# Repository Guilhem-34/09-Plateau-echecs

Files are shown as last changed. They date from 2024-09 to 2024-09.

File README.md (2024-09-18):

# High-Tech-Chess Project (In Progress)
###### {Polytech Montpellier Third year Project}

Second project of the year, currently in progress and the biggest project I've worked for !

## Introduction

Chess is a game that transcends time. That's why we wanted to innovate by using modern technologies to make the game experience more futuristic. 

What if I tell you that it's possible to play chess from a distance while physically moving pawns. This is currently our goal by making an automatic mechanism which takes in input the XY coordinates and then move the pawn.

here's how the game would be played :

   - The 1st player move his pawn and the system copy the movement in the 2nd player's chessboard.
     
   - After the movement being done, it's the 2nd player's turn, doing the same thing as the 1st player.

## Visuel
<div align="center">
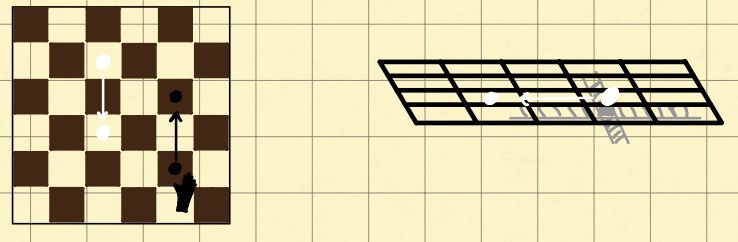
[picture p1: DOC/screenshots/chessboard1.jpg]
  
</div>

## More technically

### Board mechanism

For chess pieces, we have pieces with a magnetic disk at the base, easily found in supermarkets or on the Internet. We decided to use this feature and move them with an electromagnet by using electromagnetic force.

So we're going to use a mechanical system that moves along the carthesian plane. We're thinking in terms of a system using stepper motors, pulleys and timing belts, in the same way as CNC systems.

<div align="center">
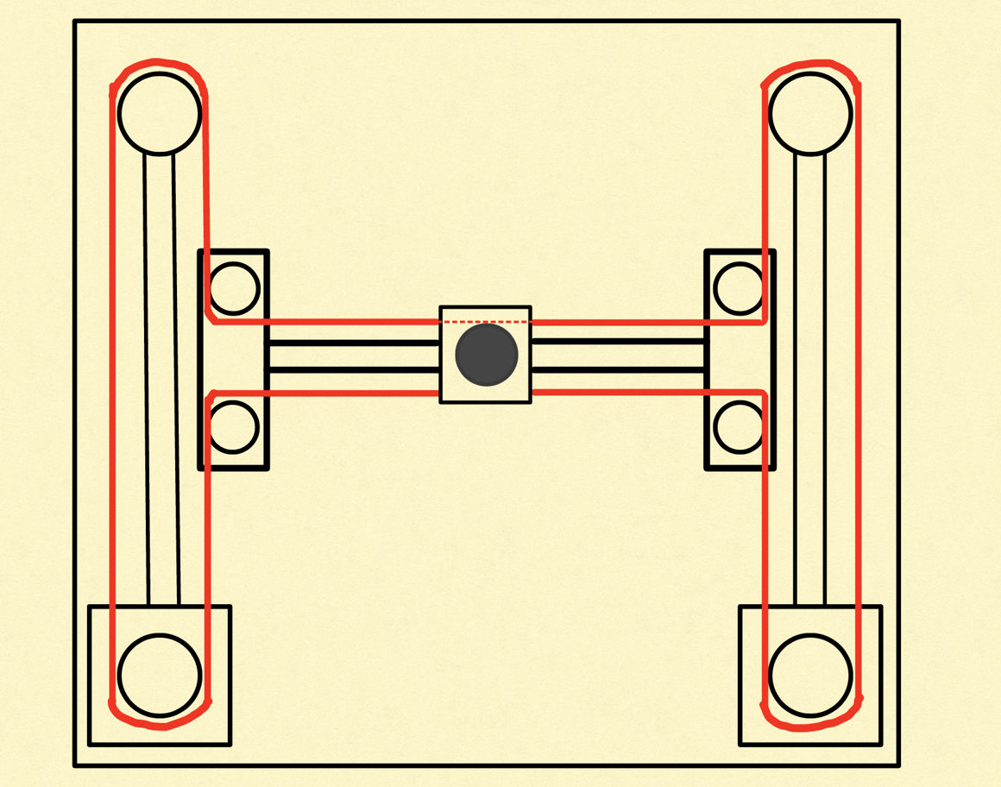
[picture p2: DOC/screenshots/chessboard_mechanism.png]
  
</div>

As someone who really likes projects needing at the same time elctronics, IT and mechanics (i.e. Mecatronic), I'm very excited to see the final result !

### Pawns detections

We have several tools and ways to detect the presence of the pawn but our first idea is to use Hall effect sensors which detects the presence of the pawn thanks to theirs base's magnet disk.

### The Microcontroller

To control all of this stuff, it'll be necessary to use a Microcontroller. We first thought of using an Arduino but we would like to change of µC because most of our last projects were including an Arduino, we want to discover something else. 

As we're learning a lot about the nucleo board from STM in our µC class, we would like to use it at the end of our project. But we need to be effective because we have a time constraint, so we decided to temporarily use the Arduino board for the tests.

## Features

At the end of our project, the High Tech Chess board will be able of :

- Determine the position of the pieces to be moved.
- From the start and finish coordinates, find the shortest path, avoiding the other pieces.
- Move eliminated pieces to one side of the board.
- Send and receive data over a network for remote play.
- Report all movements using a graphical interface.

**Stay tuned for further project updates !**

<br />
<br />

## 

<br />
<br />

Review of the 1<sup>st</sup> prototype
===========================================================

For 3 months, we worked on various aspects of our project and were able to make a few observations.

<div align="center">
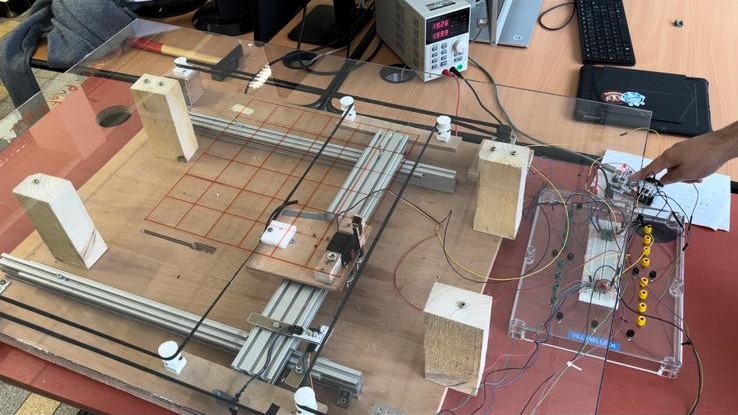
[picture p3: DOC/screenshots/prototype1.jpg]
  
</div>

### Board mechanism

As this is not our core business, we found it very difficult to create a fluid, solid and reliable mechanical system. Indeed, our system had certain imperfections, such as :

- Movement with deviations.
- A belt that wasn't tight enough (the belt therefore wasn't taking all the motor's steps).
- Very fragile pulleys, which were 3D printed.

<div align="center">
  
</div>

### Pawns detections and movement

We thought using an electromagnet to move the pawns but it turned out to be a bad idea because the pawn base's diameter is too short to close the electromagnet's field. Instead, we'll be using a simple magnet which gives more power to attract the pawns. 

### The Microcontroller

As planned from the very beginning, we performed the first tests (stepper motors and servomotor) on the Arduino development board, then wrote the function libraries directly on the STM32 board. 

In the end, the migration to STM32 proved to be an interesting choice, not only because we were able to put our knowledge into practice, but also because we were faster and more reactive. Indeed, the STM's processor frequency is much higher than the Arduino's (48 MHz for the STM32 board vs. 64kHz for the Arduino board).

In terms of code, our program can :

- Move a given number of squares in one direction.
- Go from point A to point B (only if the destination square is empty).
- Display and update the chessboard.
- Detect the interruption of the push buttons when reseting the system position's.

### To sum up

This prototype has a lot of mechanical issues, so we decided to put more efforts into the developpment of a 2<sup>nd</sup> prototype. This one will fix those issues and make it more reliable, lighter and more compact.

At this stage of the project, we're starting to have a lot of wires, so we're planning to do a PCB to make it cleaner. 

We made a lot of mistakes during the developpment of the first prototype but that's part of the process ! 

<br />
<br />

## 

<br />
<br />

Review of the 2<sup>nd</sup> prototype
===========================================================

For the last month, we designed a second prototype which (in theory) will fix the issues encountered on the first prototype.

<div align="center">
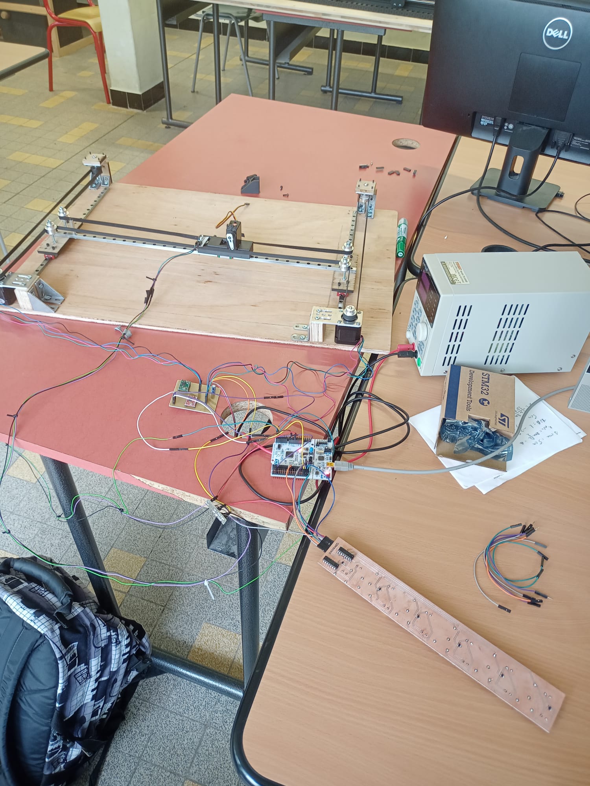
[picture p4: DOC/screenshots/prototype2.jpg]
  
</div>

### Board mechanism

This time, we made the mechanism more quickly and fix some issues but unfortunately, we've run into others issues such as :

- A bad quality of the ball bearing carriages.
- A belt that still wasn't tight enough (the belt therefore wasn't taking all the motor's steps).

However, since the beginning, we've been using a breadboard to link our peripherals to our microcontroller, which is no longer comfortable when we have a lot of cables. So we designed a PCB that makes our workspace cleaner.

<div align="center">
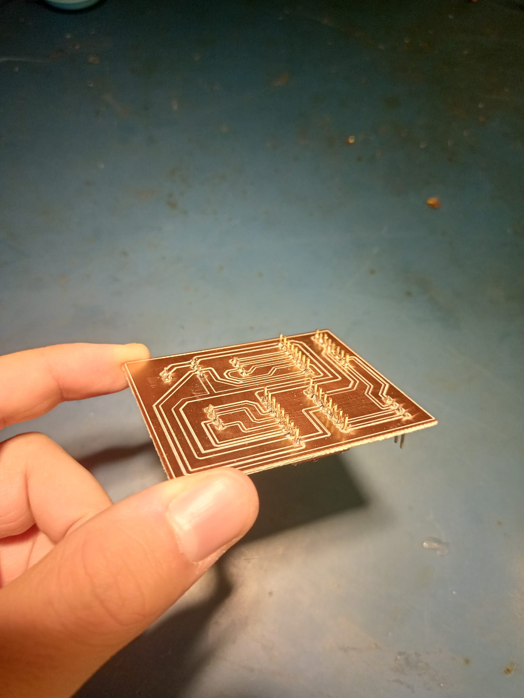
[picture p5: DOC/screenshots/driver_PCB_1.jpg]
  
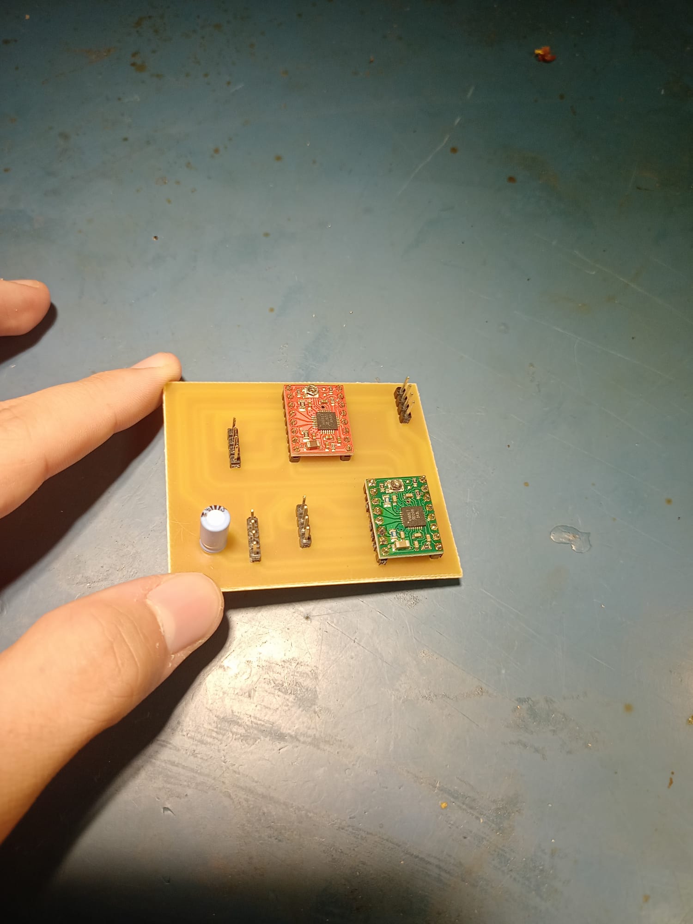
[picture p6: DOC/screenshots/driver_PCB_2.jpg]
  
</div>

### Pawns detections

As soon as we received our hall-effect sensors, we were able to test them and design a PCB. Due to a lack of time, we designed a PCB that recovers the state of each sensor on a single line of our chessboard.

Actually, we used demultiplexors to recover the state of a sensor : one which choose the sensor per line and one who select the line.

<div align="center">
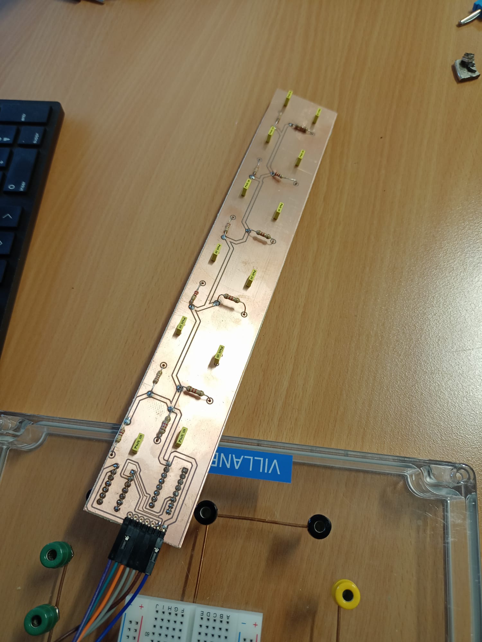
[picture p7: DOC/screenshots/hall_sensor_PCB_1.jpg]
  
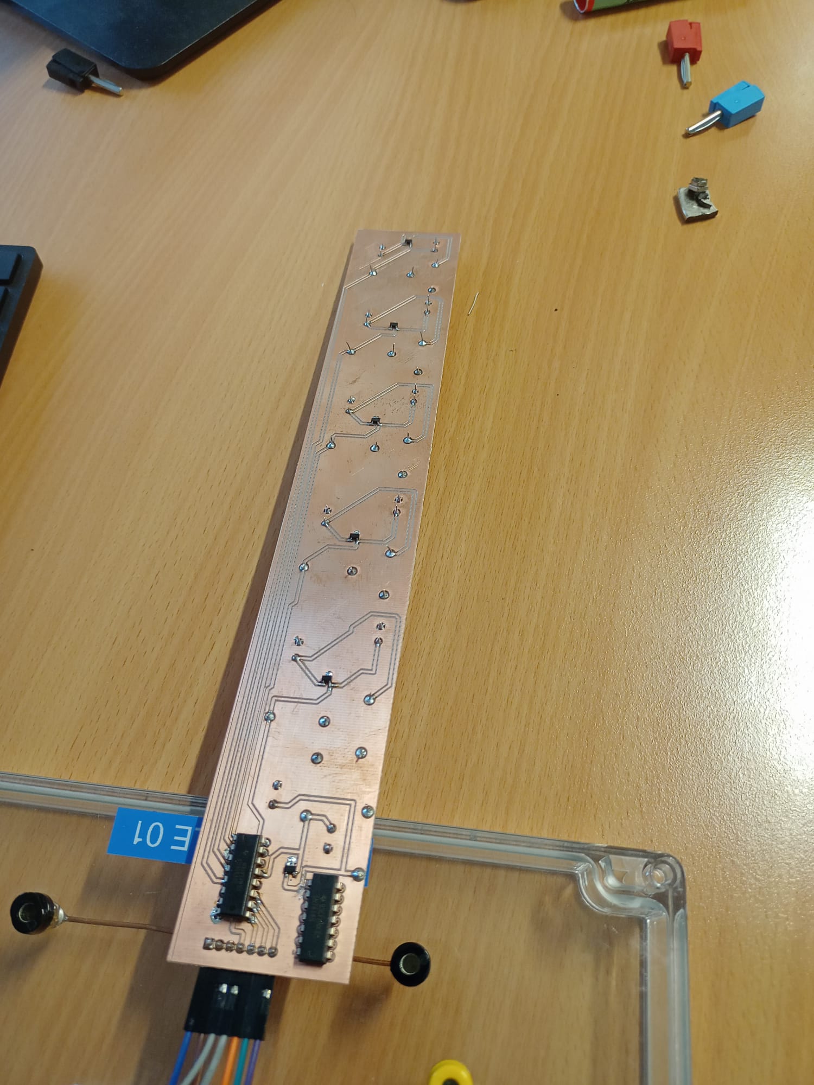
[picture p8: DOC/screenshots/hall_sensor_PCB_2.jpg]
  
</div>

### The Microcontroller

We added some functions to perform the detection through the hall effect sensors. The state of all of the sensors is displayed on a table. It would be interesting to use DMA for making the printing into console more fast and to allow the processor to do something else.

## To sum up

This prototype fixed the previous issues but still have some. Unfortunately, in the rush, we forgot to record a video of the demo.

Finally, if we were to continue this project, our objective would be to:

- Add the Enable pin to the motor drivers to enable them only when we have to move and thus avoid overheating of the motors.
- Design a shield-shaped PCB on our board to make modifications more flexible.
- Avoid lateral play of the main rail by using a T-shaped lateral structure connected to the main rail.
- Replace the demultiplexors with an I2C bus port expansion card.

At the end of this project, we've had a lot of mechanical constraints, but we've also become aware of how difficult it is to manage time. However, this project was full of interesting subjects and we learned so much things !

We'll get back stronger :)

<br/>

_ZAKANI-FADILI Bilel - ASSET Guilhem - AUBERTIN Michael_

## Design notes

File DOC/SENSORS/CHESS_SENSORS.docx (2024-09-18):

ZAKANI-FADILI Bilel

AUBERTIN Michael

ASSET Guilhem

# Choix du type de capteurs

# I. Capteur à effet Hall

## A. Présentation

### Principe : lorsqu'un courant électrique passe à travers un conducteur et qu'un champ magnétique est appliqué perpendiculairement à ce conducteur, une différence de tension se produit sur les côtés du conducteur. C’est l’effet Hall.

### Lorsqu'un champ magnétique externe est présent et qu'il coupe le conducteur, cela crée une différence de tension sur les côtés du conducteur, selon l'effet Hall. C’est cette tension qui est détectée par le capteur.

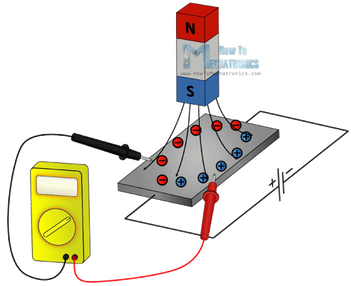
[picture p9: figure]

Après plusieurs recherches de différents capteurs, nous décidons de choisir le capteur TLE 4935 (https://www.conrad.fr/fr/p/infineon-technologies-capteur-a-effet-hall-tle-4935-l-3-5-24-v-dc-plage-de-mesure-10-20-mt-psso-3-2-a-so-153775.html) qui possède une plage de tension de 3,5 à 24 V et une plage de mesure de +10 à +20 mT, ces caractéristiques s’accordent bien avec nos besoins. Ce capteur se révèle également intéressant par son prix (0,76€ l’unité) en fonction du nombre de capteurs nécessaire.

## B. Méthode d’utilisation

Comme notre capteur doit pouvoir récupérer la position de chaque pièce sur l’échiquier, notre première idée et la plus simple est de placer un capteur à effet hall sous chaque case. On vient placer une surface plane avec nos capteurs en dessous de notre échiquier. Cette méthode permettrait d’avoir l’état de chaque case en temps réel (libre ou occupé). En revanche, comme il y a 96 cases qui peuvent accueillir les pions (64 cases jouables + 32 cases pour les pièces mangées), il faudrait donc utiliser 96 capteurs à effet hall. Comme évoqué précédemment, le capteur est avantageux à partir du moment où il est utilisé en petite quantité, contrairement à notre cas. Il faudrait débourser 72€ de capteurs ce qui est inenvisageable et rendrait le prix final du produit beaucoup trop cher.

### Nous cherchons donc une méthode pour diminuer le nombre de capteurs tout en apportant les mêmes fonctionnalités. Pour cela, nous avons pensé à deux méthodes :

### Electroaimant entouré de capteurs :

Cette méthode consiste à placer les capteurs autour de l’électroaimant. De cette manière, 8 capteurs suivent le déplacement du système mécanique et c’est celui-ci qui va se déplacer comme un serpent sur tout l’échiquier entre chaque action pour identifier l’état des cases. En revanche, cette méthode peut se révéler relativement lente et surtout très complexe à coder. En effet, si le système parcourt l’échiquier, plusieurs capteurs peuvent être amenés à identifier la même case à intervalles de temps différents. Il faut donc pouvoir accepter la mesure de certains capteurs et en rejeter d’autres.

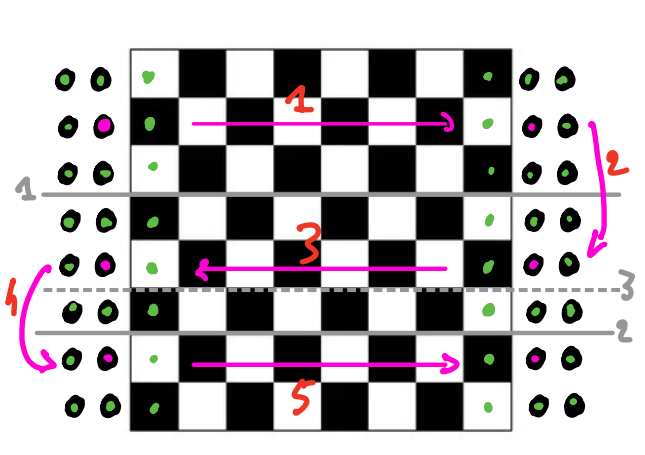
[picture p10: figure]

##### 1. Translation de 9 cases vers la droite

##### 2. Translation de 3 cases vers le bas

##### 3. Translation de 9 cases vers la gauche

##### 4. Translation de 2 cases vers le bas

##### 5. Translation de 9 cases vers la droite

### Fig 1. Déplacement du système principal entouré des capteurs

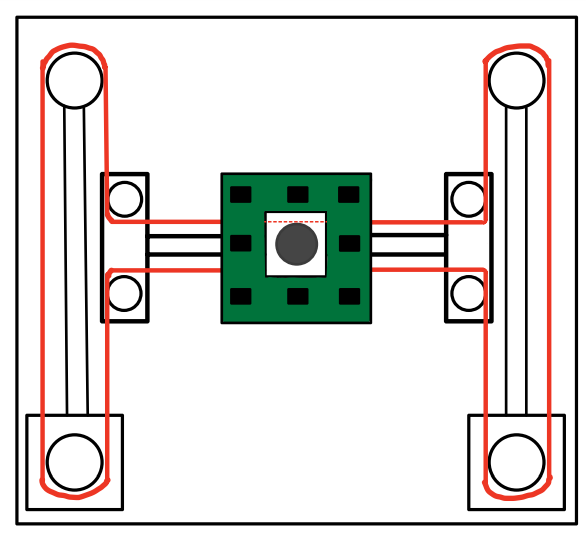
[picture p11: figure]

### Fig 2. Vue d’ensemble du système principal entouré des capteurs

### Barrette de capteurs accroché à la structure principal :

Cette méthode s’inspire de la précédente où cette fois l’objectif est de scanner chaque case une seule fois. Elle doit également garder un faible nombre de capteurs. Nous nous sommes donc inspirés du mécanisme de photocopie d’une imprimante. En effet, une barrette lumineuse effectue un seul déplacement dans un sens pour venir photocopier la feuille de papier. Le principe est le même, une barrette de 10 capteurs accrochée à la structure principale (qui se déplace uniquement linéairement) va venir scanner toutes les cases en un seul mouvement. Cette façon de faire simplifie le traitement des données tout en simplifiant le mouvement.

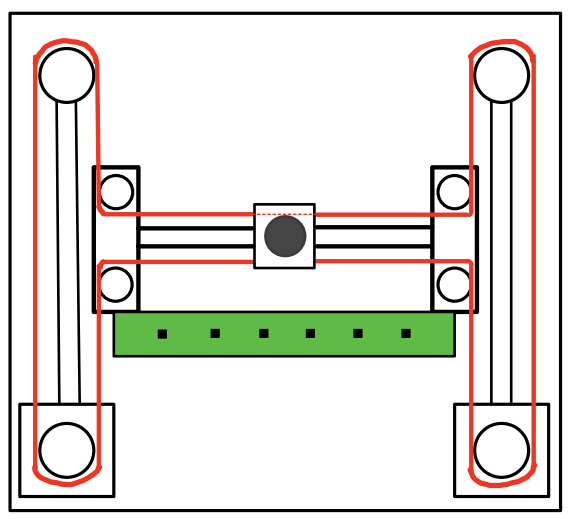
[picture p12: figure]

### Fig 3. Vue d’ensemble avec la barrette de capteurs

# II. Capteur de force FSR

## A. Présentation

### Principe : Un capteur de force FSR est un capteur plat, flexible, qui permet de mesurer la force en fonction de la pression qui y est appliquée : F=P*S

Il faut savoir que les capteurs de force ne permettent pas une lecture immédiate. En effet, il faut les étalonner à l’aide de charges de références. Les résistances de mesure de force reposent sur une technologie de piézorésistive. Autrement dit, ce sont des éléments passifs qui se comportent en résistance variable dans un circuit électrique. Comme le montre la figure 4, lorsqu'il n'est pas sollicité, le capteur présente une résistance élevée, de l'ordre de quelques mégaohms (MΩ), qui diminue lorsqu'une force est appliquée, généralement de l'ordre de quelques kiloOhms (KΩ). Si l'on considère l'inverse de la résistance (conductance), la réponse du capteur en fonction de la force appliquée est proportionnelle dans la plage de force prévue pour le modèle.

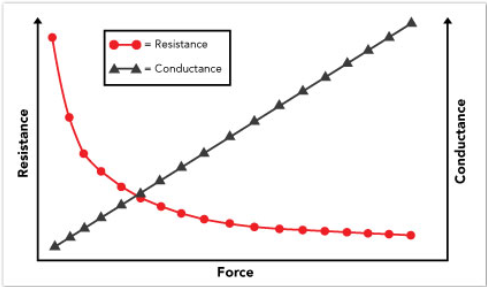
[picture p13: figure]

### Fig 4. Reponse du capteur FSR en fonction de la force

## C. Méthode d’utilisation

### Pour rappel, les capteurs doivent permettre de récupérer la position de chaque pièce sur l’échiquier. Il y a besoin d’un contact entre les pièces d’échecs et les capteurs, il faudrait placer un capteur sous chaque case, de la manière que la première méthode avec les capteurs à effet Hall.

# III. Antenne NFC

## A. Présentation

### Principe : un tag NFC fonctionne avec une technologie proche de l’induction. Le tag NFC est composé d’une antenne et d’une mémoire. L’antenne relais va émettre un champ magnétique qui va alimenter le tag et donc émettre son contenu en mémoire.

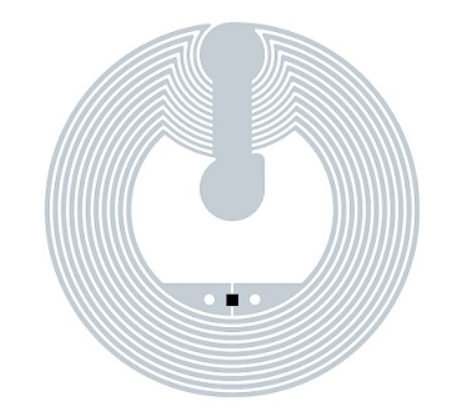
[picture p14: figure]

### Fig 5. Tag NFC

## D. Méthode d’utilisation

Cette méthode est plus particulière car elle consiste à placer un tag NFC sous chaque pièce. Le plateau d’échecs va ensuite être analysé à l’aide d’une antenne NFC accroché au système principal. De cette manière, on pourrait récupérer la position de chaque pièce en « scannant » toute les cases. Chaque pièce serait donc associée au contenu mémoire de son tag NFC.

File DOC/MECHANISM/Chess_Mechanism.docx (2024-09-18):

Asset Guilhem

Aubertin Michaël

Zakani Bilel

Mécanisme de la table

Le point de départ de notre projet reposait sur la partie mécanique, nous devions étudier les différents mécanismes qui nous permettraient de déplacer les pièces une fois la commande ordonnée par notre code. Le principe étant de pouvoir atteindre un point avec des coordonnées x et y, nous avons eu l’idée d’utiliser une machine à commande numérique (CNC).

Choix du type de CNC :

1. Core XY

La structure CNC la plus connue est le Core XY, elle est grandement utilisée dans les systèmes d’impression 3D et dans les tables d’usinage. Elle permet d’atteindre des coordonnées x et y mais ne permet pas de se déplacer selon l’axe en z.

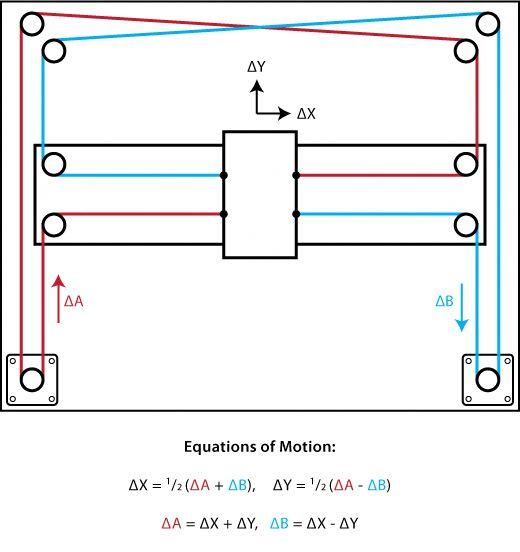
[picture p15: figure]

Schéma 1 : Core XY

A : Principe de fonctionnement

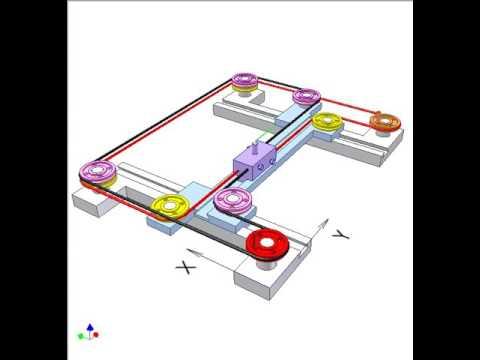
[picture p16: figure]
Controlling two linear motions of an object 3

Vidéo n°1 : Fonctionnement Core XY

Les mouvements dans le plan de la structure violette le long des axes X et Y sont contrôlés par les moteurs symbolisés dans cette vidéo par les roues rouges et oranges.

La courroie dentée noire est fixée à la plateforme violette. Elle permet de relier la roue rouge aux poulies roses.

La courroie crantée rouge est-elle aussi fixée à la plateforme. Elle relie la roue orange aux poulies jaunes.

Lorsque les moteurs rouge et orange tournent en sens inverse à la même vitesse, l'objet se déplace le long de l'axe X.

Lorsque les moteurs tournent dans le même sens à la même vitesse, l'objet se déplace le long de l'axe Y.

Lorsqu'un seul des deux moteurs tourne, l'objet violet se déplace en diagonale.

B. Avantages et inconvénients :

Points positifs :

- Précision : Le système Core XY offre une haute précision de mouvement grâce à la séparation des moteurs pour chaque axe.
- Vitesse : Ils peuvent atteindre des vitesses élevées en raison de la conception du mouvement parallèle.
- Stabilité : La structure est plus stable, ce qui peut minimiser les vibrations.

Points contraignants :

- Complexité : La mise en place et la maintenance d'un système Core XY peuvent être plus complexes en raison du nombre de composants. Une des difficultés principales sera d’aligner parfaitement la hauteur des roulements avec les différents moteurs.
- Coût : Ce système peut être plus coûteux à construire en raison du matériel supplémentaire nécessaire.

2. H-Bot

Le système H-Bot est une variante du système Core XY, cependant il possède des spécificités qui pourraient être particulièrement intéressantes pour notre projet.

A : Principe de fonctionnement :

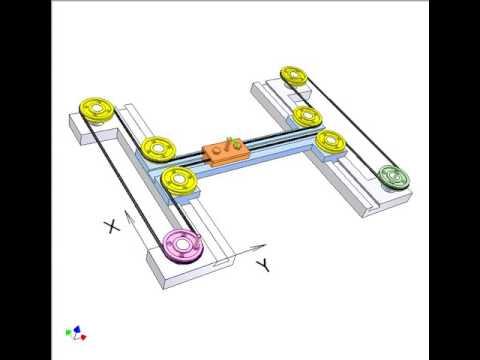
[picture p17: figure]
Controlling two linear motions of an object 1a

Vidéo n°2 : Fonctionnement H-Bot

Les mouvements de la structure orange le long des axes X et Y sont contrôlés par les moteurs représentés ici par les poulies rose et verte.

Une branche de la courroie noire est fixée au bloc orange, l'autre le traverse.

Lorsque les poulies rose et verte tournent dans des directions opposées à la même vitesse, l'objet se déplace le long de l'axe X.

Lorsque les poulies rose et verte tournent dans le même sens à la même vitesse, l'objet se déplace le long de l'axe Y.

B. Avantages et inconvénients :

Points positifs :

- Simplicité : Le système H-Bot est souvent plus simple en termes de conception et de mouvement, ce qui peut faciliter la construction et la maintenance.
- Coût : En général, il peut être moins cher à construire en raison de la conception plus simple.
- Gain de place : Ce système pourrait être particulièrement minimaliste en termes de hauteur notamment.

Points contraignants :

- Précision : Peut avoir une précision légèrement inférieure par rapport aux systèmes Core XY.
- Vitesse : Peut ne pas atteindre les mêmes vitesses que les systèmes Core XY en raison de la conception

3. Système cartésien

Le système CNC cartésien est un système amélioré du Core XY au niveau des déplacements. En effet, il permet un déplacement le long de l’axe X, Y et Z.

A : Principe de fonctionnement :

Le principe de fonctionnement est exactement le même que celui en Core XY, cependant, il permet de se mouvoir également selon l’axe Z à l’aide d’un moteur fixé sur la plateforme.

B. Avantages et inconvénients :

Points positifs :

- Les CNC cartésiennes ont principalement les mêmes points positifs que le CORE XY
- Le point fort principal de ce système est l’accessibilité au déplacement le long de l’axe Z

Points contraignants :

- La vitesse d’exécution de ce système est un peu plus lente que le Core XY
- Le principale point négatif de la machine cartésienne est que la structure principale qui se déplace le long de l’axe X est encombrée d’un moteur dont les branchements doivent être portatifs .

Tableaux de choix :

Insérer tableau

Conclusion :

Pour conclure, grâce à nos différentes recherches, nous avons récolté de nombreuses informations sur les différentes CNC qui nous ont permis de repérer les qualités et défauts de chacune. En prenant compte de nos besoins, nous pensons que la machine idéale serait la H-Bot. Elle nous permettrait d’avoir une solution peu coûteuse , plus facile à construire et surtout elle occuperait moins de place (en hauteur) ce qui permettrait d’être plus discret tout en étant efficace. Nous avons confirmé nos intentions de manière plus sérieuse en remplissant le tableau de choix (tableau précédent ) qui a confirmé nos propos.

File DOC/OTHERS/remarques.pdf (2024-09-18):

Schéma explicatif du choix de la taille des pièces (soucies de passer entres) :

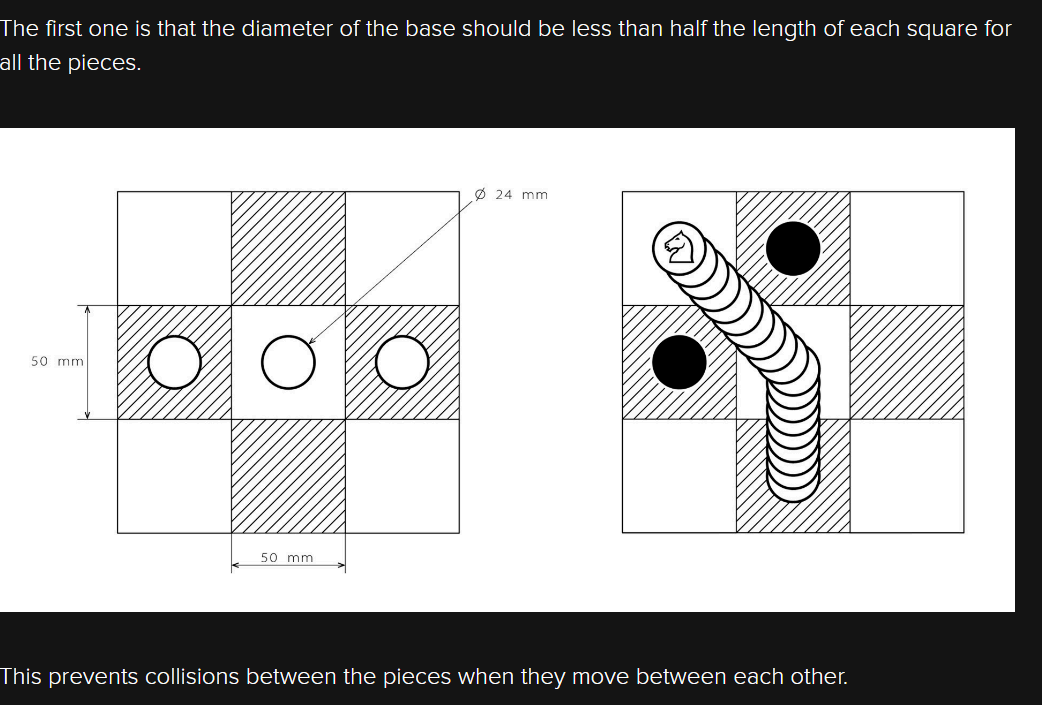
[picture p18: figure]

Force de l’aimant :

Calculer la force requise pour tirer une pièce aimantée à travers une fine plaque d'aluminium implique plusieurs facteurs, notamment la force magnétique de l'électroaimant, la distance entre l'électroaimant et la pièce, la masse de la pièce, et les caractéristiques magnétiques de la plaque d'aluminium. Voici une approche simplifiée pour estimer cela :

1. **Loi de Coulomb :** La force magnétique entre deux aimants est généralement calculée à l'aide de la loi de Coulomb magnétique. Cette loi donne la force entre deux pôles magnétiques et dépend de l'intensité magnétique, de la distance entre les aimants, et d'autres facteurs.

\[ F = \frac{{\mu_0 \cdot m_1 \cdot m_2}}{{4 \pi \cdot d^2}} \]

- \( F \) est la force magnétique.
- \( \mu_0 \) est la perméabilité du vide.
- \( m_1 \) et \( m_2 \) sont les moments magnétiques des deux aimants.
- \( d \) est la distance entre les deux aimants.
2. **Force nécessaire pour soulever la pièce :** La force magnétique devrait être suffisante pour vaincre la force gravitationnelle agissant sur la pièce.

\[ F_{\text{gravité}} = m \cdot g \]

- \( F_{\text{gravité}} \) est la force gravitationnelle.
- \( m \) est la masse de la pièce.
- \( g \) est l'accélération due à la gravité (environ \( 9.8 \, \text{m/s}^2 \)).

3. **Force nécessaire pour traverser la plaque d'aluminium :** En fonction de l'épaisseur de la plaque d'aluminium et de ses propriétés magnétiques, vous devrez également prendre en compte la force nécessaire pour traverser la plaque.

\[ F_{\text{aluminium}} = \text{...} \]

La formule exacte dépendra des propriétés spécifiques de la plaque, comme la perméabilité magnétique de l'aluminium.

4. **Force totale nécessaire :** La force totale nécessaire serait la somme de la force pour vaincre la gravité et la force pour traverser la plaque.

\[ F_{\text{totale}} = F_{\text{gravité}} + F_{\text{aluminium}} \]

Il est important de noter que ces calculs simplifiés peuvent ne pas tenir compte de tous les détails du système, et des tests expérimentaux réels peuvent être nécessaires pour affiner ces estimations. De plus, la sécurité doit être une considération importante pour éviter tout risque de dommages ou de blessures.

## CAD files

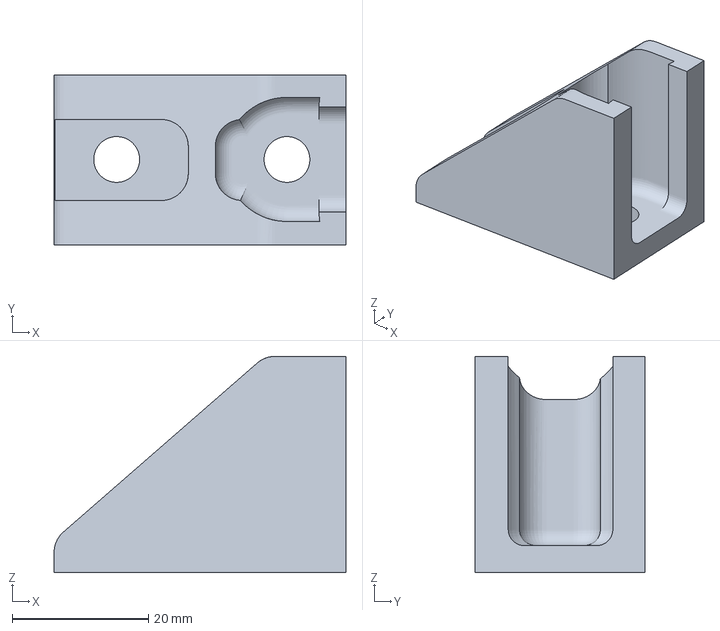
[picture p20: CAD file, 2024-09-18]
3D/SYSTEM/BELT_TENSIONER/piece3.3MF
42.9 x 25.0 x 31.7 mm

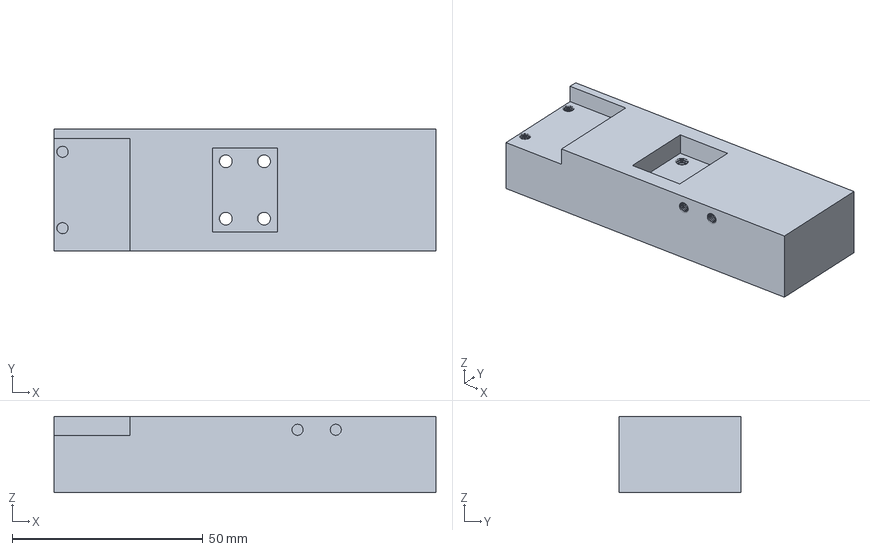
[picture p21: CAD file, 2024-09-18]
3D/SYSTEM/system.3mf
100.0 x 32.0 x 20.0 mm

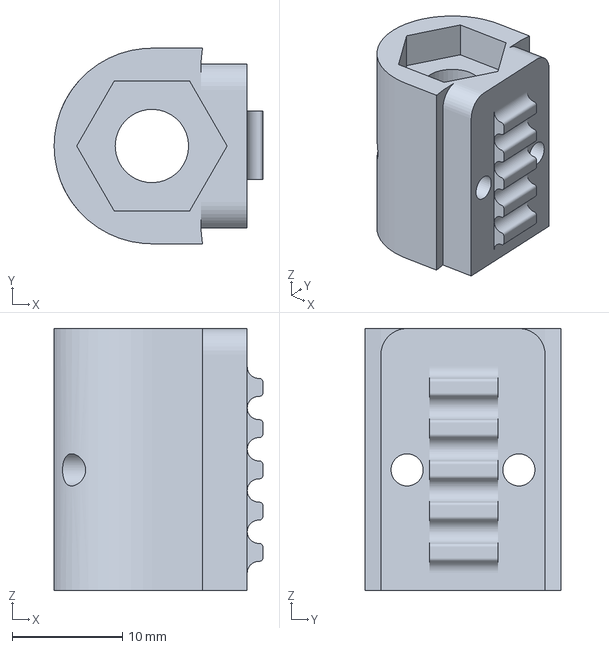
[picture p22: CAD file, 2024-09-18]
3D/SYSTEM/BELT_TENSIONER/piece2.3MF
19.0 x 17.8 x 23.8 mm

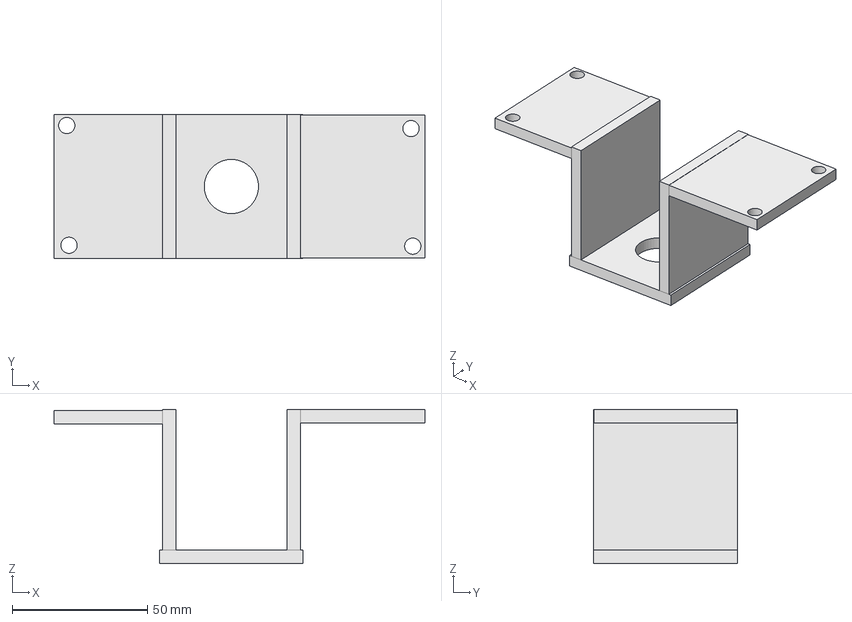
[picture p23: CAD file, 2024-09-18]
3D/MOTORS/MOTOR.FCStd
137.0 x 53.0 x 57.0 mm

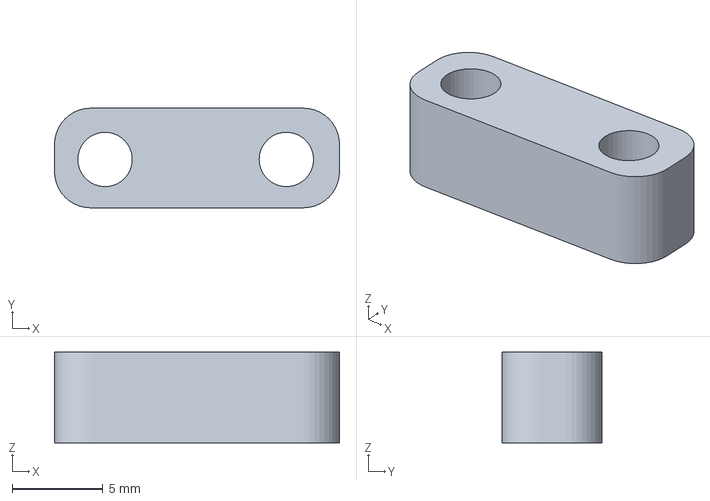
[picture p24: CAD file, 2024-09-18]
3D/SYSTEM/BELT_TENSIONER/piece1.3MF
15.7 x 5.50 x 5.00 mm

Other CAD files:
3D/MOTORS/MOTOR_echecs.step
3D/MOTORS/MOTOR-BodySketch002.3mf
3D/MOTORS/MOTOR_echecs.3mf

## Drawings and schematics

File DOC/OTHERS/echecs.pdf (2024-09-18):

# ECHECS

# objectif

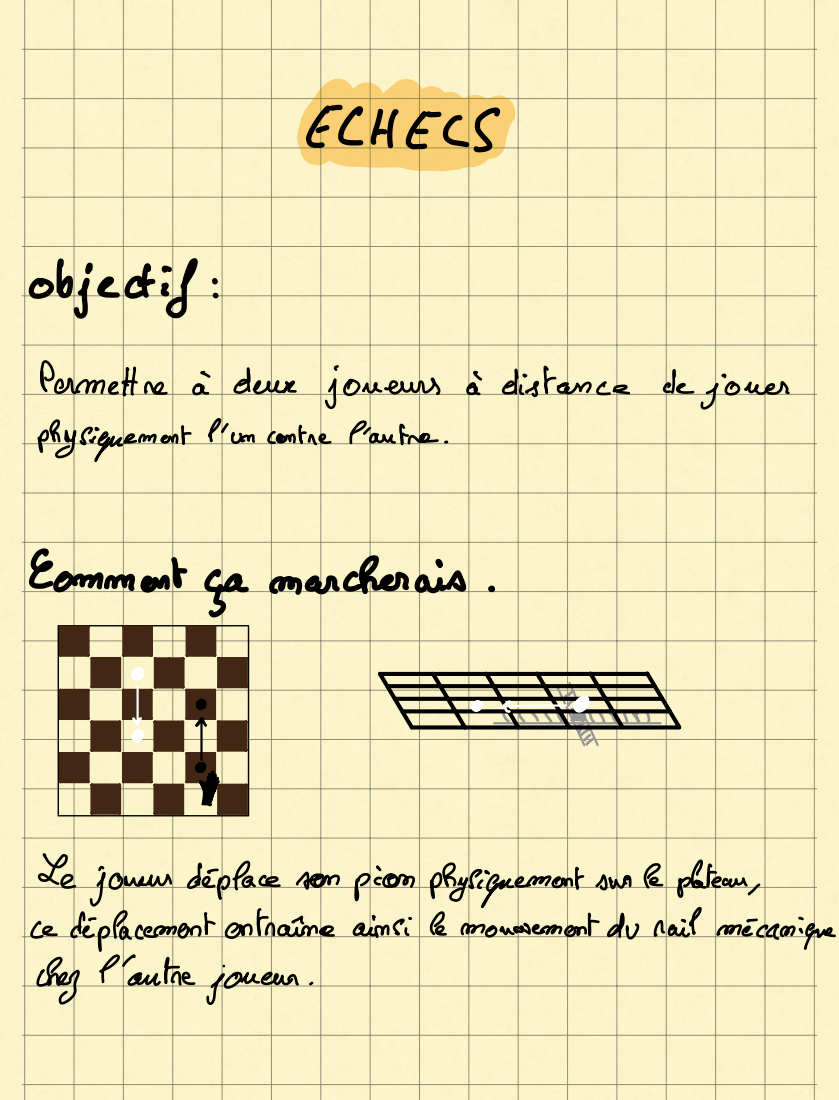
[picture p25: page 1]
Comment; ça marcherais; ce déplacemententraîne ainsi; le mouvementdu rail mécanique

Permettre | à | deux joueurs à distance de jouer

physiquement l'un contre l'autre

ja | ja | in is | ja
ja irminos | ja àItm Itm | | | ÉÉ

ja | | injmiôïramm
orm

Le joueur déplace son pion physiquement sur le plateau

chez l'autrejoueur

## Plus techniquement

Railmécanique | Plateau | Transmission
équipée d'un | | équipédecapteurs | Enréseau IUDP
déplacement | pourdétecter lapièce | | Communiquer
déplacementpar | le plus courtpour | | coorddépartetarrivée
aimant activabledésact | sous chaquecase | ou TCP entre57m32
en 2D | s | trouve le chemin déplacements successif

### cheminsdecasesde l'Gmes ou endiagonale

chaquepion

# Cahier des charges

En somme | notre | plateau | | doit pouvoir

### Déterminer la position de lapièce à déplacer

Apartirdescoordonnées | | | dedépart et d'arrivée trouver

### Déterminer letypede pièce

### lechemin lepluscourt en évitantlesautres pions

### Débarasser lespièces éliminées sur un cotéde la planche

### Envoyer et recevoir les données en réseau pour permettre

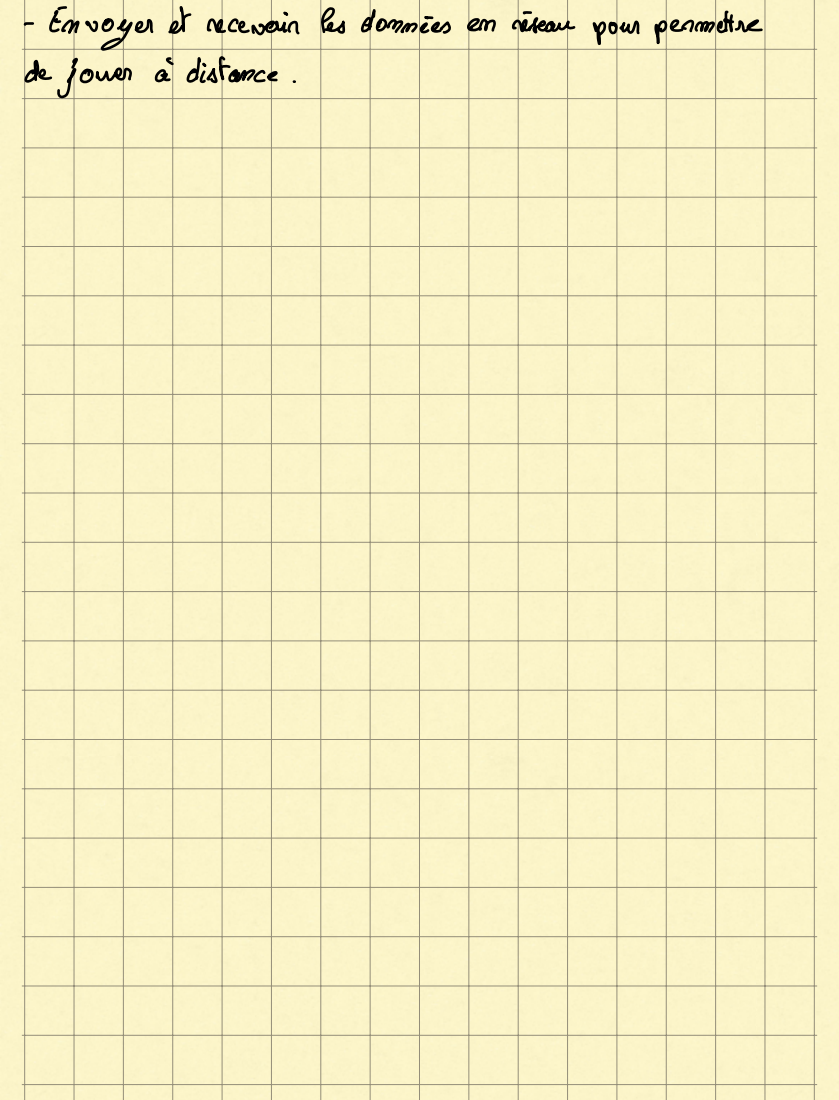
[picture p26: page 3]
dejouer à distance

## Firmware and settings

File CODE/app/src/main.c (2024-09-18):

/*
 * main.c
 *
 *  Created on: 22 February 2023
 *      Author: Laurent
 */

#include "stm32f0xx.h"
#include "main.h"
#include "bsp.h"
#include "delay.h"
#include "motor.h"
#include "chess.h"


// Static functions
static void SystemClock_Config(void);

// Global variables
uint8_t timebase_irq;
uint8_t system_delay;
uint8_t c;
uint8_t PB_BOTTOM = 0; 			//Push Button on the bottom of the board
uint8_t PB_LEFT = 0; 			//Push Button on the left of the board
uint8_t SENSOR_STATE;



uint8_t ad_lut[6] = {0,1,4,6,7,5};


// Main program
int main() {


	/*
	 * Initializations
	 */




	// Configure System Clock (48MHz)
	SystemClock_Config();

	// Configure SysTick at 10ms (10Hz) interrupt period
	while(SysTick_Config(SystemCoreClock/100) != 0);

	// Initialize console
	BSP_Console_Init();
	my_printf("Console Ready!\r\n");
	my_printf("SYSCLK = %d\r\n", SystemCoreClock);

	// Initialize LED and the 4 Push-Buttons
	BSP_LED_Init();
	BSP_PB_Init();

	// Initialize Timers Delay
	BSP_MOTORS_DELAY_TIM_init();
	BSP_PB_DELAY_TIM_init();

	// Initialize Timer for PWM output
	BSP_TIMER_PWM_Init();

	// Configure sampling timer with 10ms period (100Hz)
	BSP_TIMER_Timebase_Init(10);

	// Initialize sensors
	SENSORS_Init();

	// Initialize NVIC
	BSP_NVIC_Init();

	// Initialize Motors
	MOTORS_Init();


	// Wait  here for user button
	while(BSP_PB_GetState() == 0);


	//TIM1->CCR1 = 23;

	//Initialize Motors Position
	//MOTOR_CLEAR_POSITION();

	int board[CHESS_SIZE][CHESS_SIZE];

	Chess_Init(board);

	Print_Board(board);

	/*
	my_printf("\n\n\n-------------DEMONSTRATION STARTED-------------\r\n\n\n");

	DEMO1();

	my_printf("\n\n\n-------------DEMONSTRATION FINISHED !-------------\r\n\n\n");
	*/

	/*
	my_printf("\n\n\n-------------DEMONSTRATION STARTED-------------\r\n\n\n");


	FIND_PATH_AND_MOVE(board, 1, 0, 3, 3);

	Print_Board(board);


	FIND_PATH_AND_MOVE(board, 5, 5, 0, 2);

	Print_Board(board);


	FIND_PATH_AND_MOVE(board, 1, 4, 1, 5);

	Print_Board(board);



	my_printf("\n\n\n-------------DEMONSTRATION FINISHED !-------------\r\n\n\n");

	*/



	/*
	 *  Main Loop
	 */



	uint8_t i;
	uint8_t	sensors_buffer[6];
	my_printf("\e[2J");
	my_printf("\e[10;1H");

	while(1)
	{


		// Do every 10ms
		if(timebase_irq == 1)
		{


			for(i=0; i< 6; i++){

				sensors_buffer[i] = SENSOR_GetState(ad_lut[i]);
			}

			my_printf("Sensor 1 : %d  |  Sensor 2 : %d  |  Sensor 3 : %d  |  Sensor 4 : %d  |  Sensor 5 : %d  |  Sensor 6 : %d\n\r", sensors_buffer[1], sensors_buffer[2], sensors_buffer[3], sensors_buffer[4], sensors_buffer[5], sensors_buffer[0]);
		}
	}

}

/*
 * 	Clock configuration for the Nucleo STM32F072RB board
 * 	HSE input Bypass Mode 			-> 8MHz
 * 	SYSCLK, AHB, APB1 				-> 48MHz
 *  PA8 as MCO with /16 prescaler 	-> 3MHz
 */

static void SystemClock_Config() {
	uint32_t HSE_Status;
	uint32_t PLL_Status;
	uint32_t SW_Status;
	uint32_t timeout = 0;

	timeout = 1000000;

	// Start HSE in Bypass Mode
	RCC->CR |= RCC_CR_HSEBYP;
	RCC->CR |= RCC_CR_HSEON;

	// Wait until HSE is ready
	do {
		HSE_Status = RCC->CR & RCC_CR_HSERDY_Msk;
		timeout--;
	} while ((HSE_Status == 0) && (timeout > 0));

	// Select HSE as PLL input source
	RCC->CFGR &= ~RCC_CFGR_PLLSRC_Msk;
	RCC->CFGR |= (0x02 << RCC_CFGR_PLLSRC_Pos);

	// Set PLL PREDIV to /1
	RCC->CFGR2 = 0x00000000;

	// Set PLL MUL to x6
	RCC->CFGR &= ~RCC_CFGR_PLLMUL_Msk;
	RCC->CFGR |= (0x04 << RCC_CFGR_PLLMUL_Pos);

	// Enable the main PLL
	RCC->CR |= RCC_CR_PLLON;

	// Wait until PLL is ready
	do {
		PLL_Status = RCC->CR & RCC_CR_PLLRDY_Msk;
		timeout--;
	} while ((PLL_Status == 0) && (timeout > 0));

	// Set AHB prescaler to /1
	RCC->CFGR &= ~RCC_CFGR_HPRE_Msk;
	RCC->CFGR |= RCC_CFGR_HPRE_DIV1;

	//Set APB1 prescaler to /1
	RCC->CFGR &= ~RCC_CFGR_PPRE_Msk;
	RCC->CFGR |= RCC_CFGR_PPRE_DIV1;

	// Enable FLASH Prefetch Buffer and set Flash Latency
	FLASH->ACR = FLASH_ACR_PRFTBE | FLASH_ACR_LATENCY;

	// Select the main PLL as system clock source
	RCC->CFGR &= ~RCC_CFGR_SW;
	RCC->CFGR |= RCC_CFGR_SW_PLL;

	// Wait until PLL becomes main switch input
	do {
		SW_Status = (RCC->CFGR & RCC_CFGR_SWS_Msk);
		timeout--;
	} while ((SW_Status != RCC_CFGR_SWS_PLL) && (timeout > 0));

	/*--- Use PA8 as LSE output ---*/

	// Set MCO source as LSE
	RCC->CFGR &= ~RCC_CFGR_MCO_Msk;
	RCC->CFGR |= RCC_CFGR_MCOSEL_LSE;     // Change here

	// No prescaler
	RCC->CFGR &= ~RCC_CFGR_MCOPRE_Msk;

	// Enable GPIOA clock
	RCC->AHBENR |= RCC_AHBENR_GPIOAEN;

	// Configure PA8 as Alternate function
	GPIOA->MODER &= ~GPIO_MODER_MODER8_Msk;
	GPIOA->MODER |= (0x02 << GPIO_MODER_MODER8_Pos);

	// Set to AF0 (MCO output)
	GPIOA->AFR[1] &= ~(0x0000000F);
	GPIOA->AFR[1] |= (0x00000000);

	// Update SystemCoreClock global variable
	SystemCoreClockUpdate();
}


void DEMO1(void){

	MOVE_STRAIGHT("UP", 5);
	MOVE_STRAIGHT("RIGHT", 1);
	MOVE_STRAIGHT("DOWN", 5);
	MOVE_STRAIGHT("RIGHT", 1);
	MOVE_STRAIGHT("UP", 5);
	MOVE_STRAIGHT("RIGHT", 1);
	MOVE_STRAIGHT("DOWN", 5);
	MOVE_STRAIGHT("RIGHT", 1);
	MOVE_STRAIGHT("UP", 5);
	MOVE_STRAIGHT("RIGHT", 1);
	MOVE_STRAIGHT("DOWN", 5);
}


void DEMO2(void){

	MOVE_STRAIGHT("RIGHT", 5);
	MOVE_STRAIGHT("UP", 1);
	MOVE_STRAIGHT("LEFT", 5);
	MOVE_STRAIGHT("UP", 1);
	MOVE_STRAIGHT("RIGHT", 5);
	MOVE_STRAIGHT("UP", 1);
	MOVE_STRAIGHT("LEFT", 5);
	MOVE_STRAIGHT("UP", 1);
	MOVE_STRAIGHT("RIGHT", 5);
	MOVE_STRAIGHT("UP", 1);
	MOVE_STRAIGHT("LEFT", 5);
}


void DEMO3(void){

	MOVE_STRAIGHT("RIGHT", 5);
	MOVE_STRAIGHT("LEFT", 5);
	/*
	MOVE_STRAIGHT("RIGHT", 5);
	MOVE_STRAIGHT("LEFT", 5);
	MOVE_STRAIGHT("RIGHT", 5);
	MOVE_STRAIGHT("LEFT", 5);
	*/
}

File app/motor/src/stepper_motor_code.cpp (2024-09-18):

// Include the AccelStepper library:
#include "AccelStepper.h"


// Include stepper motor functions

// Define stepper motor connections and motor interface type.  
// Motor interface type must be set to 1 when using a driver
#define dirPin 2
#define stepPin 3
#define stepsPerRevolution 200


void setup() {

  Serial.begin(9600);

  pinMode(6,OUTPUT);
  pinMode(7,OUTPUT);
  pinMode(8,OUTPUT);
  pinMode(10,INPUT);

  pinMode(stepPin, OUTPUT);
  pinMode(dirPin, OUTPUT);
  
  digitalWrite(6,LOW);
  digitalWrite(7,LOW);
  digitalWrite(8,HIGH);


  
  }

  

void loop(){


  Serial.print(digitalRead(10));

  /*

  for(int i = 0; i < 5*stepsPerRevolution; i++){
    digitalWrite(stepPin, HIGH);
    delayMicroseconds(500);
    digitalWrite(stepPin, LOW);
    delayMicroseconds(500);
    
  }

  delay(1000);
  
  
  stepper.setCurrentPosition(0);

  while( stepper.currentPosition() != 400){
    stepper.setSpeed(3200);
    stepper.runSpeed();
  }


  delay(200);

  stepper.setCurrentPosition(0);

  while( stepper.currentPosition() != -100){
    stepper.setSpeed(-700);
    stepper.runSpeed();
  }

  

  delay(800);

  */
}

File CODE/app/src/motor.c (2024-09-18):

/*
 * motor.c
 *
 *  Created on: 3 févr. 2023
 *      Author: Laurent
 */

#include "motor.h"
#include "bsp.h"
#include "main.h"

uint16_t 	STEP_DELAY = 1200;
uint8_t		STEPS_PER_REVOLUTION = 200;
uint16_t 	CLEAR_STEPS_NUMBER = 5000;
extern uint8_t PB_BOTTOM;		//line 0
extern uint8_t PB_LEFT;			//line 1



/*
 * void MOTORS_Init()
 * Initialize Motors pins such as Step and Direction Pins for left and right motors
 *
 * LEFT MOTOR :
 * 		Step Pin	(PC2)
 * 		Dir Pin		(PC3)
 *
 * RIGHT MOTOR :
 * 		Step Pin	(PC4)
 * 		Dir Pin		(PC5)
 *
 * All pins are in GPIO Output Mode
 *
 */

void MOTORS_Init(){

	// Enable GPIOC clock
	RCC->AHBENR |= RCC_AHBENR_GPIOCEN;

	// Configure PC2, PC3, PC4 and PC5 as output
	GPIOC->MODER &= ~GPIO_MODER_MODER2_Msk;
	GPIOC->MODER |= (0x01 << GPIO_MODER_MODER2_Pos);

	GPIOC->MODER &= ~GPIO_MODER_MODER3_Msk;
	GPIOC->MODER |= (0x01 << GPIO_MODER_MODER3_Pos);

	GPIOC->MODER &= ~GPIO_MODER_MODER4_Msk;
	GPIOC->MODER |= (0x01 << GPIO_MODER_MODER4_Pos);

	GPIOC->MODER &= ~GPIO_MODER_MODER5_Msk;
	GPIOC->MODER |= (0x01 << GPIO_MODER_MODER5_Pos);

	// Configure PC2, PC3, PC4 and PC5 as Push-Pull output
	GPIOC->OTYPER &= ~GPIO_OTYPER_OT_2;
	GPIOC->OTYPER &= ~GPIO_OTYPER_OT_3;
	GPIOC->OTYPER &= ~GPIO_OTYPER_OT_4;
	GPIOC->OTYPER &= ~GPIO_OTYPER_OT_5;

	// Configure PC2, PC3, PC4 and PC5 as High-Speed Output
	GPIOC->OSPEEDR &= ~GPIO_OSPEEDR_OSPEEDR2_Msk;
	GPIOC->OSPEEDR |= (0x03 << GPIO_OSPEEDR_OSPEEDR2_Pos);

	GPIOC->OSPEEDR &= ~GPIO_OSPEEDR_OSPEEDR3_Msk;
	GPIOC->OSPEEDR |= (0x03 << GPIO_OSPEEDR_OSPEEDR3_Pos);

	GPIOC->OSPEEDR &= ~GPIO_OSPEEDR_OSPEEDR4_Msk;
	GPIOC->OSPEEDR |= (0x03 << GPIO_OSPEEDR_OSPEEDR4_Pos);

	GPIOC->OSPEEDR &= ~GPIO_OSPEEDR_OSPEEDR5_Msk;
	GPIOC->OSPEEDR |= (0x03 << GPIO_OSPEEDR_OSPEEDR5_Pos);

	// Disable PC2, PC3, PC4 and PC5 Pull-up/Pull-down
	GPIOC->PUPDR &= ~GPIO_PUPDR_PUPDR2_Msk;
	GPIOC->PUPDR &= ~GPIO_PUPDR_PUPDR3_Msk;
	GPIOC->PUPDR &= ~GPIO_PUPDR_PUPDR4_Msk;
	GPIOC->PUPDR &= ~GPIO_PUPDR_PUPDR5_Msk;

	// Set Initial State OFF
	GPIOC->BSRR = 0x00000000;
}




/*
 * void MOTOR_LEFT_ENABLE(){
 *
 * LEFT motor enable with a defined direction using STEP_DELAY
 *
 */

void MOTOR_LEFT_ENABLE(uint16_t STEPS_NUMBER, int8_t DIR){


	// Set direction to clockwise if DIR=1 and counterclockwise if DIR=(-1)
	if(DIR == 1){
		GPIOC->BSRR |= GPIO_BSRR_BS_3;
	}
	else{
		GPIOC->BSRR |= GPIO_BSRR_BR_3;
	}

	// Spin the right motor till the number of steps is reached
	for(int i = 0; i < STEPS_NUMBER; i++){
		GPIOC->BSRR |= GPIO_BSRR_BS_2;
		BSP_MOTORS_DELAY_TIM_us(STEP_DELAY);
		GPIOC->BSRR |= GPIO_BSRR_BR_2;
		BSP_MOTORS_DELAY_TIM_us(STEP_DELAY);
	}

}





/*
 * void MOTOR_RIGHT_ENABLE(){
 *
 * Right motor enable with a defined direction using STEP_DELAY
 *
 */

void MOTOR_RIGHT_ENABLE(uint16_t STEPS_NUMBER, int8_t DIR){


	// Set direction to clockwise if DIR=1 and counterclockwise id DIR=(-1)
	if(DIR == 1){
		GPIOC->BSRR |= GPIO_BSRR_BS_5;
	}
	else{
		GPIOC->BSRR |= GPIO_BSRR_BR_5;
	}


	// Spin the right motor till the number of steps is reached

	for(int i = 0; i < STEPS_NUMBER; i++){
		GPIOC->BSRR |= GPIO_BSRR_BS_4;
		BSP_MOTORS_DELAY_TIM_us(STEP_DELAY);
		GPIOC->BSRR |= GPIO_BSRR_BR_4;
		BSP_MOTORS_DELAY_TIM_us(STEP_DELAY);
	}

}





/*
 * void MOTORS_ENABLE(){
 *
 * Enable both motors with defined steps and directions using TIM2 = STEP_DELAY as step delay
 *
 */

void MOTORS_ENABLE(uint16_t LEFT_STEPS_NUMBER, int8_t LEFT_DIR, uint16_t RIGHT_STEPS_NUMBER, int8_t RIGHT_DIR){


	// Set left motor's direction to clockwise if LEFT_DIR=1 and counterclockwise if LEFT_DIR=(-1)
	if(LEFT_DIR == 1){
		GPIOC->BSRR |= GPIO_BSRR_BS_3;
	}
	else{
		GPIOC->BSRR |= GPIO_BSRR_BR_3;
	}


	// Set right motor's direction to clockwise if RIGHT_DIR=1 and counterclockwise if RIGHT_DIR=(-1)
	if(RIGHT_DIR == 1){
		GPIOC->BSRR |= GPIO_BSRR_BS_5;
	}
	else{
		GPIOC->BSRR |= GPIO_BSRR_BR_5;
	}


	uint8_t 	complete = 0;
	uint8_t 	motor_state = 0;



	while(!complete){





		switch(motor_state){



			case 0 :											// Make a step with both motors


				if(RIGHT_STEPS_NUMBER == 0){					// All right motor steps completed before left motor
					motor_state = 1;
					break;
				}
				else if(LEFT_STEPS_NUMBER == 0){					// All left motor steps completed before right motor
					motor_state = 2;
					break;
				}


				GPIOC->BSRR |= GPIO_BSRR_BS_2;					// Write a HIGH into left motor's step pin
				GPIOC->BSRR |= GPIO_BSRR_BS_4;					// Write a HIGH into right motor's step pin
				BSP_MOTORS_DELAY_TIM_us(STEP_DELAY);
				GPIOC->BSRR |= GPIO_BSRR_BR_2;					// Write a LOW into left motor's step pin
				GPIOC->BSRR |= GPIO_BSRR_BR_4;					// Write a LOW into right motor's step pin
				BSP_MOTORS_DELAY_TIM_us(STEP_DELAY);


				LEFT_STEPS_NUMBER--;
				RIGHT_STEPS_NUMBER--;

				break;



			case 1 :											// Make a step with left motor only

				if(LEFT_STEPS_NUMBER == 0 ){					// All right motor steps completed before left motor
					complete = 1;
					break;
				}

				MOTOR_LEFT_ENABLE(LEFT_STEPS_NUMBER,LEFT_DIR);
				complete = 1;
				break;



			case 2 :											// Make a step with right motor only

				if(RIGHT_STEPS_NUMBER == 0 ){					// All right motor steps completed before left motor
					motor_state = 1;
					break;
				}
				MOTOR_RIGHT_ENABLE(RIGHT_STEPS_NUMBER,RIGHT_DIR);
				complete = 1;
				break;

		}
	}
}




/*
 * void MOTOR_CLEAR_POSITION(){
 *
 * Clear the motors position by leading the system at the bottom-left of the board.
 *
 * Note that for a movement like this one, the right motor always turn counterclockwise.
 *
 * Wherever our system is, we'll say that it needs  at least 5000 steps to return to its initial position.
 *
 */
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
